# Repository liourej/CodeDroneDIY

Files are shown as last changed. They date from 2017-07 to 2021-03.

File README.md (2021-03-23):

# <p align="center">DIY flight controller from scratch</p>

<p align="center">
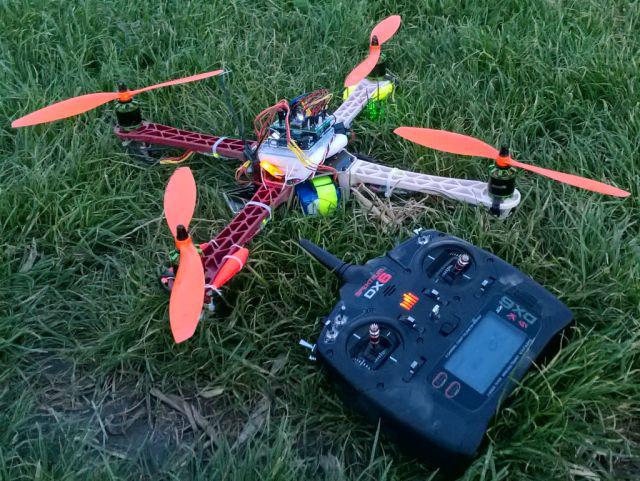
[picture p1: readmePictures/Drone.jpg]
    
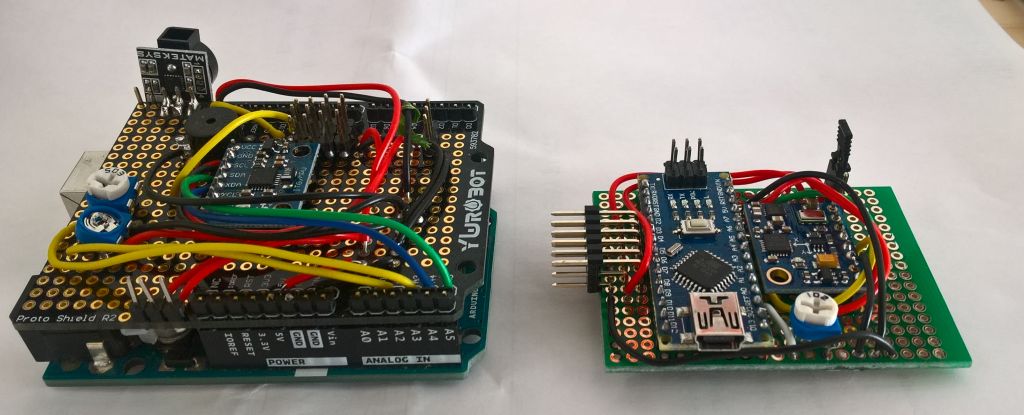
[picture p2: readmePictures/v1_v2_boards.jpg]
    
    Pictures: First hardware version using Arduino Uno board and second hardware version using Arduino Nano board
</p>

---------------------------Table of contents----------------------------

[**1. Introduction**](#intro)

1.1. Purpose

1.2. Progress state

1.3. Videos

[**2. Required sensors**](#requiredSensors)

[**3. Accro mode explained (aka manual)**](#accroMode)

3.1. Angle feedback

3.2. Speed stabilization

[**4. Angle mode explained (aka automatic leveling mode)**](#angleMode)

4.1. Angles and angular speeds feedback

4.2. Stabilization

[**5. Hardware configuration**](#hardwareConfiguration)

5.1. Components list

5.2. Connexions

[**6. Software setup**](#softwareSetup)

6.1 Using Arduino IDE

6.2 Using PlatformIO

6.3. Using Docker

[**7. Software detailed design**](#softwareDetailedDesign)

7.1 Source Code overview

7.2 The state machine

7.3 Radio reception

7.4 Motors speed control

7.5 Failsafe

[**8. Appendix**](#appendix)

8.1 My BenchTest

8.2 Exemple of First Person View configuration(FPV)

[**10. Glossary**](#glossary)

[**11. Bibliography**](#bibliography)

-------------------------------------------------------------------
## Warning

<p align="center">

</p>

Before starting this project, you must know that spinning propellers are very dangerous for your eyes and people around.
When using the benchtest indoor, you must wear large protective glasses, and set up a power limit.
For outside tests, choose a very large area, with nobody around.

<p align="center">
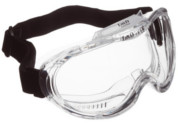
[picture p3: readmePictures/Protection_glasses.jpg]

</p>

## 1. Introduction 
### 1.1 Purpose
The aim of this project is to develop a very simple quadrirotor flight controller from scratch, using an Arduino and inertial sensors.
There is two benefits:
* to understand UAV flight stabilization
* to have our own system, with no limits for customization: you can add all the sensors you want.

In this project, the two main flight modes are addressed:
* Accrobatic mode (or manual mode): the simplest to code, but it requires flight skills
* Angle mode: more complex to implement, but easier to fly: UAV automatically goes back to
horizontal

I strongly advice to start by implementing the accrobatic mode, since a good accro mode will be a solid fundation
for angle mode, and it is easy and fast to implement.

### 1.2 Progress state
Releases have been successfully tested during flights tests: I have some nice flights in FPV on a
450mm frame, both in accro and angle modes.
BUT, this project is sometimes updated, mainly for code format, and unfortunately, I cannot realize flight tests for each submit.
So, I cannot garantee that the last commit will allow to flight without some corrections.

Note that you may also have to tune PID according to your configuration.

I advice you to use a large frame (450mm for exemple), because it is more stable, and I did not test the software on smaller frames.

### 1.3 Videos

<a href="https://www.youtube.com/watch?v=niiIYhLCFx0" target="_blank" rel="noopener noreferrer">Loop control indoor test</a>

<a href="https://www.youtube.com/watch?v=C8MZH-K4qus" target="_blank" rel="noopener noreferrer">Outdoor flight test</a>

## 2. Required sensors 

An IMU (aka MPU) is the only sensor needed for flight.

An « Inertial Measurement Unit » is a MEMS, "Microelectromechanical system", composed by a 3 axis gyroscope sensor, and 3 axis accelerometer sensor.

| IMU sensor | Function |Pros | Cons |
| --- | --- | --- | --- |
| Gyroscope | Measure angular speeds around each axis (°/sec) | Fast | Drift along time |
| Accelerometer | Measure linear acceleration on each axis (g) | Slow |  Noizy and not usable when UAV is moving |

<p align="center">
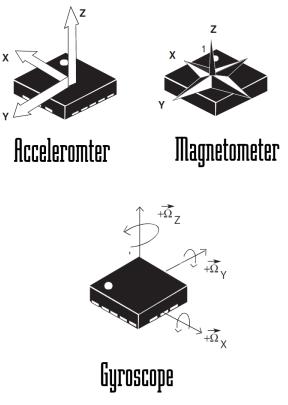
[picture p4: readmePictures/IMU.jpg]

</p>

## 3. Accro mode (aka manual) 

Accrobatic mode implements minimal stabilization algorithms to make flight possible. UAV is not able to auto-leveling, and pilot skills are required.

This mode is the required base for the angle mode, and is easier to realize: do not try to code angle mode if accro mode is not working fine.

### 3.1 Compute angle speed feedback

Accrobatic mode algorithm only needs UAV angular speeds and angular speed command as entry data. Angular speeds are computed from raw gyroscope data integration.

Exemple of pitch angle speed computation using gyroscopes:
```
// currentPitch = previousPitch + rawSensorPitch*loopTime
_pos[0] = _pos[0] + (accGyroRaw[0+3]/GyroSensitivity)*_loop_time;
```
### 3.2 Speed stabilization  

A closed-loop system is needed to control angular speed.

This system compares angular speed command to angular speed feedback, and computes a new motor power to apply.

<p align="center">
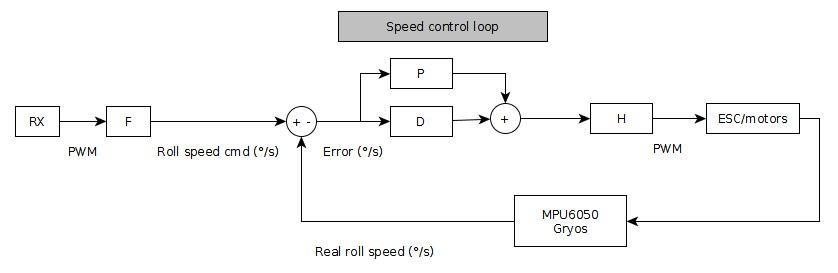
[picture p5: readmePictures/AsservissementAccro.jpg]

</p>

## 4. Angle mode (aka automatic leveling mode) 

It is a more sophisticated flight mode than the accrobatic mode: now, UAV is able to auto-level.

Auto-leveling mode entry data is UAV attitude: the angles from the horizontal (roll, pitch, yaw) and the angular speeds.

### 4.1 Compute angles and angular speeds feedback

Both angles speed and angles are required to compute reliable attitude angle feedback along time.

Both gyroscopes and accelerometers are involved.

#### 4.1.1 IMU gyroscopes

As seen previously, Angular speeds are computed from raw gyroscope data integration.

#### 4.1.1 IMU accelerometers

Attitude angles are computed from accelerations:

When UAV is not moving, or if it is moving at constant speed, accelerometers measure gravity, ie
vertical acceleration.
Angle between UAV and the gravity vector is computed by trigonometry.
Be carefull, this measure is faulty when UAV accelerates.

Exemple of pitch attitude angle computation using accelerometers:

```
_pos[0] = atan(accGyroRaw[1]/accGyroRaw[2]))*(180/PI);
```

#### 4.1.2 Data merging: the complementary filter

Complementary filter merges gyroscopes and accelerometers data, to get both sensors benefits, and to reduce theirs drawbacks:

* The gyroscope if fast but it drifts along time.

* Accelerometers are not fast enougth, they are noizy, and they are usable only when the UAV is not moving, and when UAV receive only earth acceleration.

The complementary filter mask their respective errors:

- A low-pass filter is applied on accelerometer data to filter the noize and the unwanted accelerations: these data are usefull on a long time period, fast changes have to be eliminated.
- A high-pass filter is applied on the gyrosope data: these data are usefull on short time period, but they drift and accumulate errors on long time periods.

<p align="center">
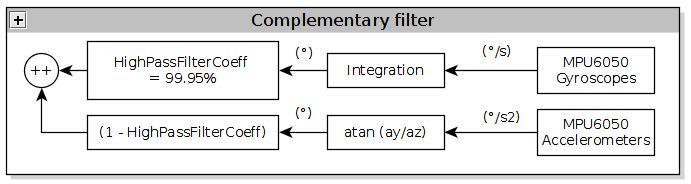
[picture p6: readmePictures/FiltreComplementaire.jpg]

</p>

**Coding exemple**

  ```
 _pos[0] = HighPassFilterCoeff*(_pos[0] + (accGyroRaw[0+3]/GyroSensitivity)*_loop_time) +
 (LowPassFilterCoeff)*((atan(accGyroRaw[1]/accGyroRaw[2]))*(180/PI));
```

Note: LowPassFilterCoeff = 1 - HighPassFilterCoeff

**Coefficients computation**

HighPassFilterCoeff is computed from the Time constant.

Time constant is a compromise between UAV acceleration filtering, and gyroscopes drift:
* Too low, accelerometer noize are not eliminated
* Too high, gyroscopes drift is not compensated

```
timeConstant = (HighPassFilterCoeff*dt) / (1-HighPassFilterCoeff)
=> HighPassFilterCoeff = timeConstant / (dt + timeConstant)
```

Time constant in this project is set to 5 milliseconds. It implies a coefficient "HighPassFilterCoeff" of 0.9995 for a loop time of 2.49 ms.

**Note:** More efficient filters like the Kalman one are used in UAV, but they are more complicated to understand, and we want a very simple DIY software!

### 4.2 Stabilization

A double closed-loop system is needed to control attitude angles. It consists of a speed closed-loop [like the one in the accro mode], inside a position closed-loop.

This system compares angle command to angle feedback, and computes a new motor power to apply. Angular feedback is computed using a complementary filter to merge gyroscope dans accelerometer data.

The pilot controls each attitude angle, and if transmitter sticks are centered, command is 0°, and UAV automatically goes back to horizontal.

<p align="center">
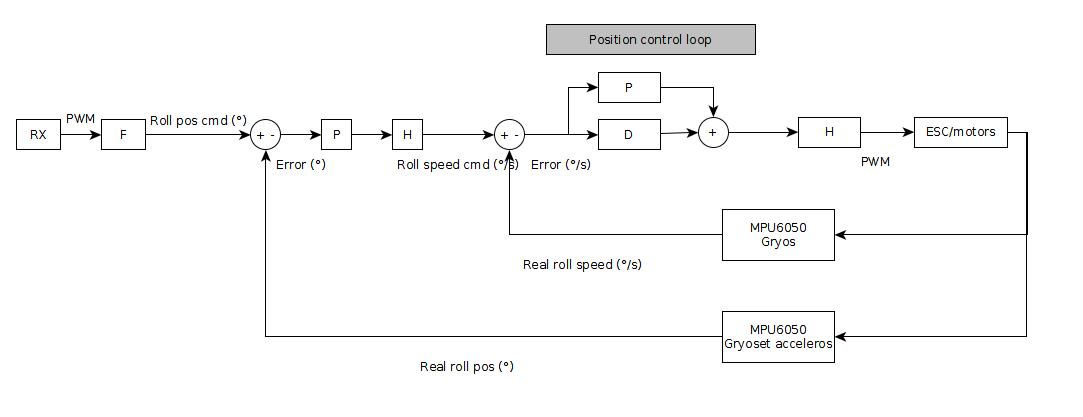
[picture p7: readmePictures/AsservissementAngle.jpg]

</p>

## 5. Hardware configuration 

### 5.1 Components list

As exemple, my hardware configuration for a 450mm quad:

| Component | Reference |
| --- | --- |
| **Microcontroller board** | Arduino Nano/Uno (ATmega328P MCU) |
| **ESC** | Afro 20A-Simonk firmware 500Hz, BEC 0.5A 1060 to 1860 us pulse width |
| **Motors** | Multistar 2216-800Kv 14 Poles - 222W Current max: 20A Shaft: 3mm 2-4S|
| **Propellers** | 10x4.5 SF Props 2pc CW 2 pc CCW Rotation (Orange) |
| **Battery** | Zippy Flightmax 3000mAh 4S |
| **Receiver** | OrangeRx R617XL CPPM DSM2/DSMX 6 ch |
| **IMU** | MPU6050 (GY-86 breakout board)|
| **Compass** | HMC5883L (GY-86 breakout board) |
| **Buzzer** | Matek lost model beeper - Built-in MCU |
| **Frame** | Diatone Q450 Quad 450 V3. 450 mm wide frame choosen for better stability and higher autonomy (the lower the size, the lower the stability).|

### 5.2 Connexions
TODO: add receiver in schematic

**Full view:**

<p align="center">
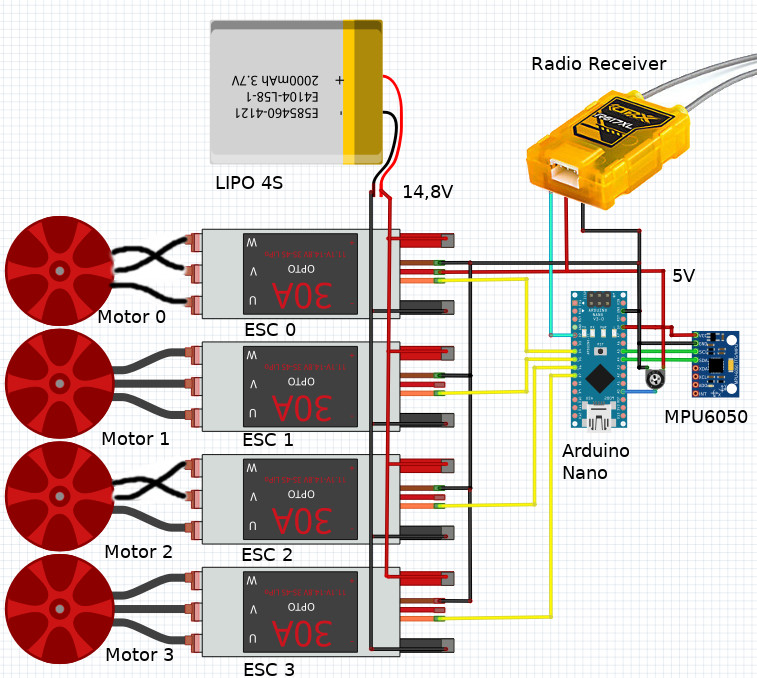
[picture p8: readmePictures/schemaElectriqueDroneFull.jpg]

</p>

**Zoomed view:**

<p align="center">
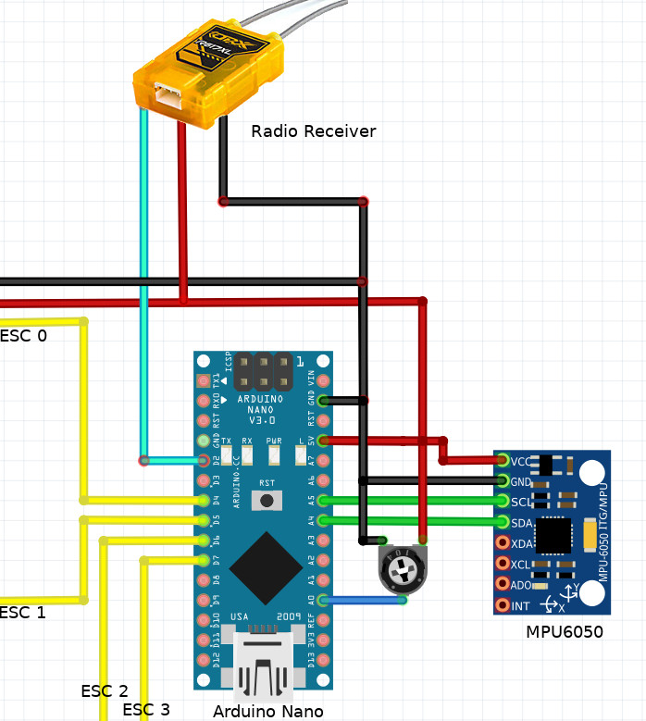
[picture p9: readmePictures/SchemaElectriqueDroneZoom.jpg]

</p>

| Arduino pin | Component |
| --- | --- |
| PD2 | receiver |
| PD4 | ESC0 |
| PD5 | ESC1 |
| PD6 | ESC2 |
| PD7 | ESC3 |
| PC0 | potentiometer |
| PC4 | SDA MPU6050 |
| PC5 | SCL MPU6050 |

<p align="center">
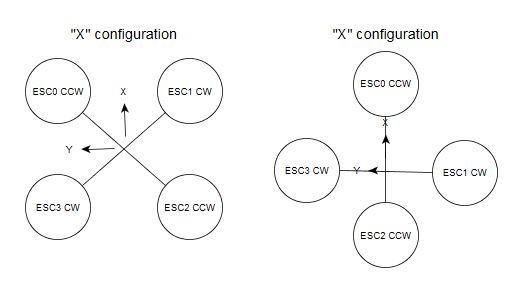
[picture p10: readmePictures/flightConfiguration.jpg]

</p>

## 6. Software setup 

### 6.1 Using Arduino IDE
With minor modifications, project can be build using Arduino IDE:
* rename "main.cpp" to "CodeDroneDIY.ino"
* copy all source files from "CodeDroneDIY/src" to "CodeDroneDIY"
* launch and compile "CodeDroneDIY.ino" using Arduino IDE

### 6.2. Using Visual Studio Code IDE and PlatformIO

* Install Visual Studio code

* Start VSCode and click on "Extensions" icon

* Install PlatformIO IDE

### 6.3. Using  Linux terminal and PlatformIO
PlatformIO is an open source ecosystem for IoT development.

#### 6.2.1. PlatformIO installation
```sudo apt-get update
sudo apt-get install python-pip
sudo pip install --upgrade pip && sudo pip install -U platformio==3.5.2
platformio platform install atmelavr --with-package=framework-arduinoavr
platformio lib install MPU6050
pio lib install "I2Cdevlib-MPU6050"
```

Optional, for code format:

```sudo apt-get install -y clang-format```

#### 6.2.2. Build project
```platformio run```

#### 6.2.3. Flash target
```platformio upload --upload-port/ttyACM0 ```

#### 6.2.4. Run unit tests

```
platformio test -e uno --verbose
```

### 6.4. Using Docker and PlatformIO
The development tool "Docker" is a container platoform: it is a stand-alone, executable package
of a piece of software that includes everything needed to run it: code, runtime, system tools,
 system libraries, settings. It isolates software from its surroundings.
* Install Docker
* Move inside docker's folder: ```cd docker```
* Build docker image: ```make image```
* Format code: ```make format-all```
* build project: ```make build-codedronediy```

## 7. Software detailed design 

### 7.1 Source code overview

<p align="center">
<img src="/readmePictures/DiagrammeUML.jpg"/>
</p>

**StateMachine folder:**

| File      | Description      |
| -------------- | -------------- |
| StateMachine.h | Contains current state |
| states/IState.h | Interface for the states (mother class)|
| states/AccroMode.cpp/h | Computes stabilization for accro mode |
| states/AngleMode.cpp/h | Computes stabilization for angle mode|
| states/Disarmed.cpp/h | Sets motors to idle |
| states/Initializing.cpp/h | Computes offsets |
| states/Safety.cpp/h | Sets motors to idle |

**Stabilization folder:**

| File      | Description      |
| -------------- | -------------- |
| hardware/InertialMeasurementUnit.cpp/h | Read roll, pitch, yaw angles from MPU6050 |
| hardware/MotorsSpeedControl.cpp/h | Manage an ESC: PWM to set |
| hardware/RadioReception.h | Receives CPPM signal acquisition using INT0 |
| Stabilization.cpp/h | Computes and apply new command from receiver sticks and current attitude |
| ControlLoop.cpp/h | Proportionnal, integral, derivative loop correction |

**customLibs folder:**

| File      | Description      |
| -------------- | -------------- |
| CustomMath.h | Mathermatical functions: mean and delta max computations|
| CustomTime.h | To measure loop time and elapsed time |
| CustomSerialPrint.h | Custom serial print to enable or disable printing|

### 7.2 The state machine

Due to security reasons, the UAV cannot start running with a flight mode enabled. Five states are defined to enable or disable flight mode safely. These states are ruled by a statemachine.

The five StateMachine states:

<p align="center">
<img src="/readmePictures/MachineEtats.jpg"/>
</p>

| State      | Description      |
| -------------- | -------------- |
| Initialization | UAV must be on the ground, horizontal, and not moving. Sensors offsets are computed. Then, if receiver switch is disarmed, the system changes to the next state. |
| Disarmed | Throttle is disabled. When the receiver switch is set to a flight mode, the system changes to the corresponding state.|
| AngleMode/AccroMode | Throttle is enabled, flight can start. After 5 seconds of power idle, the system is set to "safety" state. |
| Safety | Throttle command is disabled and power is cut. To re-arm, switch to disarmed, then choose the flight mode accroMode or angleMode |

### 7.3. Radio reception

A CPPM receiver is used to fly the UAV using a remote control.

CPPM (Pulse Position Modulation) reception  allows to receive all channels using only one entry pin. Each rising edge correpond to the end of the previous channel impulsion, and at the beginning of the next channel impulsion.
Elapsed time between two rising edge correspond to the pulse width of a given channel.

<p align="center">
<img src="/readmePictures/CPPM.jpg"/>
</p>

In this projet, each pulse width is measured using INT0, and then stored in the correponding channel of an array.

### 7.4 Motors speed control

Each motor is controlled by an ESC. The microcontroller drives the 4 ESC.

<p align="center">
<img src="/readmePictures/Afro20Amp-ESC.jpg" width="20%"/>
</p>

Motor speed is tuned by modifying the pulse width on the ESC signal wire. A pulse must be send at least every 20ms.

* Max motor speed is set by a pulse of 1860ms

* Motor is stopped by a pulse of 1060ms

All speeds between this two values are possible.

Each timer1 interrupt call the function "SetMotorsSpeed", which generate a falling edge on the previous motor and a rising edge on the current motor:

<p align="center">
<img src="/readmePictures/MotorsControl.jpg" width="60%"/>
</P>

### 7.5 Failsafe

For security, you must set the failsafe to cut motors power when radio link is lost.

To set the failsafe:
1. Put transmitter sticks in the configuration wanted when reception is lost
2. Bind the receiver with the transmitter

Transmitter configuration used during the « bind » operation defines the « failsafe. »

## 8. Appendix 

### 8.1 The benchtest

<p align="center">
<img src="/readmePictures/BenchTest01.jpg" width="40%"/>
</p>

### 8.2 FPV - First Person View  

My cheap configuration:

| Component      | Reference      |
| -------------- | -------------- |
| **Googgles** | Quanum DIY FPV Goggle V2 Pro |
| **Googgles battery** | 1000 mAh 3S |
| **Receiver** | Eachine RC832 Boscam FPV 5.8G 48CH Wireless AV Receiver  |
| **Receiver antenna** | DYS FPV 5.8G Antenna 4dBi Mushroom Antenna RHCP TX RX |
| **Camera** | Foxeer XAT600M HS1177 600TVL CCD 2.8MM IR Mini FPV Camera IR Blocked 5-22v |
| **Camera antenna** | Realacc 5.8G 5dBi 50W RHCP Omnidirectional 3 Leaf Clover FPV Antenna Red |
| **Video transmitter** | Upgrade Aomway Mini 5.8Ghz 200mW 32CH AV Wireless Transmitter Module |

## 10. Glossary 

**ESC** Electronic Speed Control

**PID** It is a Proportionnal Integral Derivative control loop

**IMU** Inertial Measurement Unit

**MPU** Motion Processor Unit

**FPV** First Person View

## 11. Bibliography 

* Arduino

https://www.arduino.cc/en/Reference/Libraries.html

https://www.arduino.cc/en/Reference/HomePage

* PWM

https://librepilot.atlassian.net/wiki/display/LPDOC/PWM,+PWMSync,+Oneshot+Output

http://forum.arduino.cc/index.php?topic=46487.0

* PPM

http://frskytaranis.forumactif.org/t4426-tuto-pwm-cppm-ccpm-ppm-s-bus-s-port-kesako

* PID

http://www.fpv-passion.fr/docteur-pid/

* Quadricopter

https://www.mondrone.net/fabriquer-quadricoptere-la-propulsion/

* Data processing

https://ericjformanteaching.wordpress.com/2013/10/08/smoothing-sensor-input/

* Data merging

http://www.mouser.fr/applications/sensor_solutions_mems/

http://www.pieter-jan.com/node/11

* Programme python

Andy BAKER

http://pythonfiddle.com/andy-baker-quadcopter/

* Vibrations

http://ardupilot.org/plane/docs/common-vibration-damping.html

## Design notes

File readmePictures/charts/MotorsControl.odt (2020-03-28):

Motor0 Motor1 Motor2 Motor3 Motor0 Timer Interrupt Timer Interrupt Timer Interrupt Timer Interrupt Timer Interrupt Timer Interrupt ticks ticks ticks PD4 (V) PD5 (V) PD6 (V) PD7 (V) ticks Motor1 Timer Interrupt

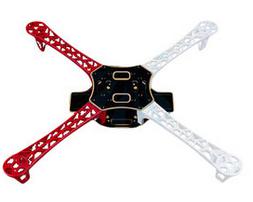
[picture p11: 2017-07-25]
readmePictures/Chassis.jpg

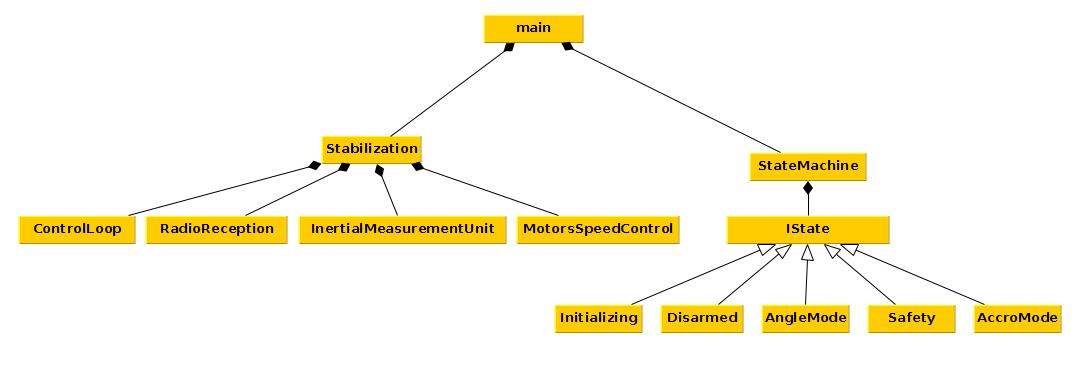
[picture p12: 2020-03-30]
readmePictures/DiagrammeUML.jpg

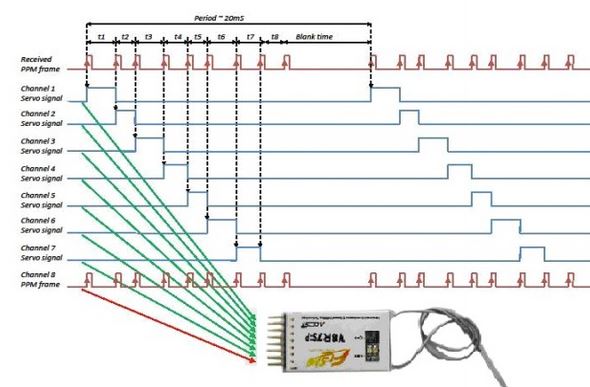
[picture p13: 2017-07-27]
readmePictures/CPPM.JPG

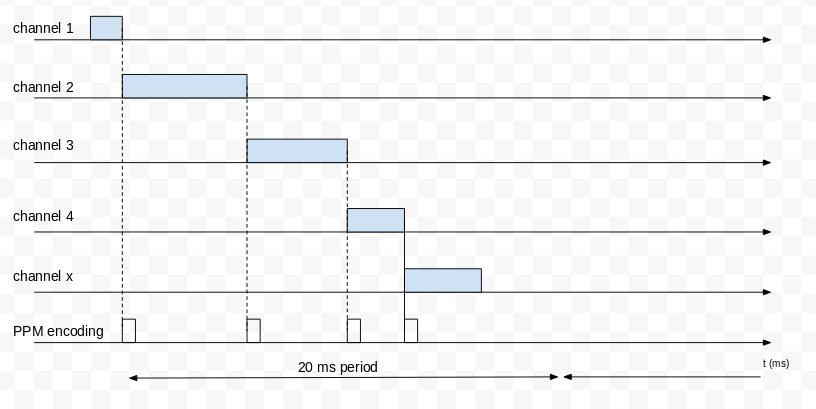
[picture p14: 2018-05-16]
readmePictures/CPPM.jpg

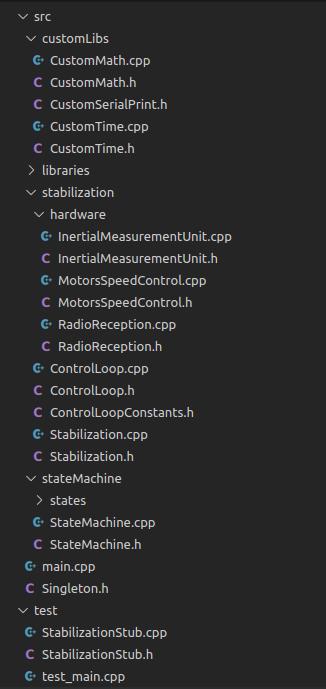
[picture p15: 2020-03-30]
readmePictures/CodeTree.jpg

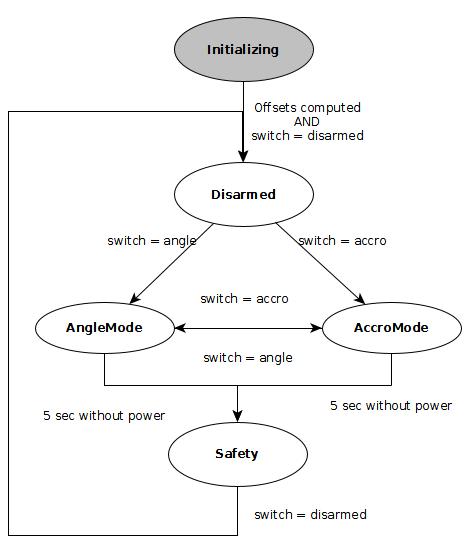
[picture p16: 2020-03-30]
readmePictures/MachineEtats.jpg

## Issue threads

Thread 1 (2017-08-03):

Wiring

2black0, 2017-08-03:
Can you share the wiring?
or any board can be to test this directly?

liourej, 2018-05-02:
The code can be run on any board using ATmega328P (Arduino Uno, Nano).
Wiring:

Arduino pin | Component
PD2 | receiver
PD4 | ESC0
PD5 | ESC1
PD6 | ESC2
PD7 | ESC3
PC0 | potentiometer
PC4 | SDA MPU6050
PC5 | SCL MPU6050

Closed 2018-05-02.

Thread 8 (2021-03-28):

Raspberry Pico

pschatzmann, 2021-03-28:
Thanks for your project. this is great work.

I am trying to use your project on a Raspberry Pico. The only AVR specific functionality is in MotorsSpeedControl so I need to provide an alternative implementation.

I have one small doubt with the  void MotorsSpeedControl::UpdateSpeed(int _id, float _PWM) method.

Is the _PWM argument the pulse width (in the range of MIN_POWER - MAX_POWER ? Or is it something else ?

The naming and data type got me a little bit confused...

pschatzmann, 2021-03-29:
I have an implementation now: https://github.com/pschatzmann/pico-arduino/blob/main/examples/codedronediy
I hope I did not get it wrong...

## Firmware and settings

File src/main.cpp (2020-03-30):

#ifndef UNIT_TEST
#include <avr/wdt.h>
#include <math.h>

#include "customLibs/CustomTime.h"
#include "stabilization/hardware/RadioReception.h"
#include "stabilization/Stabilization.h"
#include "stateMachine/StateMachine.h"

CustomTime time;
Stabilization stabilization;
StateMachine stateMachine;
void PrintConfig();

// Initialiaze all sensors and communication pipes
void setup() {
    CustomSerialPrint::begin(230400); // Console print: initialize serial communication

    stabilization.Init();
    time.Init();
    stateMachine.Init();

    wdt_enable(WDTO_1S); // Set watchdog reset
    PrintConfig();
}

// Main loop
void loop() {
    float loopTimeSec = 0.0;
    uint16_t loopNb = 0;
    float meanLoopTime = 0.0;

    loopTimeSec = time.GetloopTimeMilliseconds();

    // State Machine Initializing -> Ready -> AngleMode/AccroMode -> Safety -> Disarmed -> AngleMode/AccroMode
    stateMachine.Run(loopTimeSec);

    // Compute mean loop time and complementary filter time constant
    int flyingMode = stabilization.GetFlyingMode();
    if ((flyingMode == angleMode) || (flyingMode == accroMode)) {
        if (!stabilization.IsThrottleIdle()) {
            time.ComputeMeanLoopTime(loopTimeSec, meanLoopTime, loopNb);
        }
    }
    wdt_reset();
}

void PrintConfig() {
    if ((stabilization.GetMotorsMaxPower() == 1860)
        && (stabilization.GetMotorsMaxThrottle() >= (1860 * 0.8)))
        CustomSerialPrint::println(
                F("!!!!!!!!!!!!!!!!!!!!FLYING MODE "
                  "POWER!!!!!!!!!!!!!!!!!!!!!!!!!!!!!!!!!!!! "));
    else if ((stabilization.GetMotorsMaxPower() <= 1300))
        CustomSerialPrint::println(F("DEBUG MODE POWER!!! "));
    else
        CustomSerialPrint::println(F("UNEXPECTED POWER "));

    CustomSerialPrint::print(F("MAX_POWER: "));
    CustomSerialPrint::print(stabilization.GetMotorsMaxPower());
    CustomSerialPrint::print(F(" MAX_THROTTLE_PERCENT: "));
    // CustomSerialPrint::println(stabilization.GetMotorsMaxThrottlePercent());
    CustomSerialPrint::println(F("Setup Finished"));
}
#endif

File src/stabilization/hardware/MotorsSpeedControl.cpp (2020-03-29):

#include "MotorsSpeedControl.h"

int MotorsSpeedControl::currMotor = -1;
uint16_t MotorsSpeedControl::motorsTicks[nbMotors] = {0, 0, 0, 0};

void MotorsSpeedControl::Init() {
    // Set motors pin PD4, PD5, PD6, PD7 as outputs
    DDRD |= (1 << DDD7)| (1 << DDD6)| (1 << DDD5)| (1 << DDD4);
    InitTimer1();
    Idle();
}

// Timer interrupt to set PWM to motors controllers
typedef enum { _timer1, _Nbr_16timers } timer16_Sequence_t;

static inline void handle_interrupts(timer16_Sequence_t timer, volatile uint16_t *TCNTn,
                                     volatile uint16_t *OCRnA) {
    MotorsSpeedControl::ApplySpeed(TCNTn, OCRnA);
}

// Timer 1 is use to drive motors using PWM
SIGNAL(TIMER1_COMPA_vect) {
    handle_interrupts(_timer1, &TCNT1, &OCR1A);
}

// Timer 1 is use to drive motors using PWM
void MotorsSpeedControl::InitTimer1() {
    TCCR1A = 0;         // normal counting mode
    TCCR1B = _BV(CS10); // no prescaler
    TCNT1 = 0;          // clear the timer count
    OCR1A = usToTicks(MIN_POWER);

    TIFR1 |= _BV(OCF1A);   // clear any pending interrupts;
    TIMSK1 |= _BV(OCIE1A); // enable the output compare interrupt
}

void MotorsSpeedControl::Idle() {
    for (int id = 0; id < nbMotors; id++)
        motorsTicks[id] = usToTicks(MIN_POWER);
}

void MotorsSpeedControl::UpdateSpeed(int _id, float _PWM) {
    if (_PWM < MIN_POWER) {
        motorsTicks[_id] = usToTicks(MIN_POWER);
    } else if (_PWM > MAX_POWER) { // Check max power
        CustomSerialPrint::println(F("WARNING, MAX POWER REACHED!!"));
        motorsTicks[_id] = usToTicks(MAX_POWER);
    } else {
        motorsTicks[_id] = usToTicks(_PWM);
    }
}

// Set a falling edge for the previous motor, and a rising edge for the current motor
// Motor speed is managed by the pulse with: the larger the high level is, the faster the motor run
void MotorsSpeedControl::ApplySpeed(volatile uint16_t *TCNTn, volatile uint16_t *OCRnA) {
    static bool firstLoop = true;
    if (firstLoop) {
        currMotor = 0;
        PORTD = B00010000;
        firstLoop = false;
    }

    if (currMotor == Motor0) { // Rising edge for Motor0, and falling edge for Motor3
        PORTD ^= B00110000; // Reset pin PD4 and set pin PD5 using XOR
        *OCRnA = motorsTicks[currMotor + 1]; // When TCNTn matches OCRnA, an output compare interrupt is thrown.
    } else if (currMotor == Motor1) {// Rising edge for Motor1, and falling edge for Motor0
        PORTD ^= B01100000; // Reset pin PD5 and set pin PD6 using XOR
        *OCRnA = motorsTicks[currMotor + 1];// When TCNTn matches OCRnA, an output compare interrupt is thrown.
    } else if (currMotor == Motor2) {// Rising edge for Motor2, and falling edge for Motor1
        PORTD ^= B11000000; // Reset pin PD6 and set pin 7 using XOR
        *OCRnA = motorsTicks[currMotor + 1];// When TCNTn matches OCRnA, an output compare interrupt is thrown.
    } else {// Rising edge for Motor3, and falling edge for Motor2
        PORTD ^= B10010000; // Reset pin PD7 and set pin PD4 using XOR
        currMotor = -1;
        *OCRnA = motorsTicks[currMotor + 1];// When TCNTn matches OCRnA, an output compare interrupt is thrown.
    }
    *TCNTn = 0; // Reset timer counter
    currMotor++;
}

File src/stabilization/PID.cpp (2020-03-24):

#include "PID.h"
void PID::SetGains(const float _params[4]) {
    G = _params[0];
    Kp = _params[1];
    Kd = _params[2];
    Ki = _params[3];
}

void PID::Reset() {
    errorPrev = 0;
    integrator = 0;
}

int PID::ComputeCorrection(float _cmd, float _pos, float _loopTime) {
    error = _cmd - _pos;
    integrator = integrator + error;
    int correction =
            (int)(G * (Kp * error + Kd * ((error - errorPrev) / (_loopTime)) + Ki * integrator));

    errorPrev = error;

    // Correction in us
    return correction;
}

void PID::PrintGains(void) {
    Serial.print("G: ");
    Serial.print(G);
    Serial.print(" Kp: ");
    Serial.print(Kp);
    Serial.print(" Kd: ");
    Serial.print(Kd);
    Serial.print(" Ki: ");
    Serial.println(Ki);
}

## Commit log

2017-05-23 Correct wrong pitch correction sign
2017-05-23 Correct negative sign on pitch speed
2017-05-26 Use switch H to activate yaw PID
2017-05-28 After flight fail, set much better PID coeff
    [Reception.h]
2017-05-28 Add loop mean comp: PID coeff depends itgit add . (1.7ms in this version)
2017-05-29 Adjust angle mode PID parameters
2017-06-01 Add missing yaw reset
2017-06-03 Release for flight test - TODO: Investigate why - on pitch pos
2017-06-11 Add a safety power cut on 5th channel and code cleaned
2017-06-12 Add safety switch with safety cut after 5sec. Need cleaning!
2017-06-13 Create a state machine to encapsulate safety cut code
2017-06-24 Add buzzer activated by H switch
2017-06-27 Add IMU self-test to check IMU is working
2017-07-05 Move PID init into state machine
2017-07-08 IMU checking before flight working fine.
2017-07-08 Buzzer working with motor PWM timer at the same time
2017-07-08 Correct sign in pitch attitude computation
    [GetPosition.cpp]
2017-07-09 Complementary filter coef proportional to quadri moving probability
2017-07-09 Compute a better filter time constant. Remove changing constant.
2017-07-14 Much better filter time constant: 5sec (coeff 0.9995)
2017-08-10 Correct out of range array bug
    [Reception.h]
2017-08-19 Linux Arduino makefile working
2017-08-26 New Arduino Nano board
2017-09-02 Add a percentage thsld on throttle cmd, independant from max motor pwr thsld
2017-10-26 Update readme schematics
2017-10-28 Correct but in function used to reset PID when throttle idle
2017-10-28 Rem auto baro detection: not working because no I2C timeout
    [Attitude.cpp]
2017-10-28 Tune PIDs for 220mm racer frame
2017-10-29 Add potentiometer on A0 to tune yaw Kp on the field
2018-03-07 Add electrical schematic (WIP)
2018-05-02 Restore IMU checking at startup
2018-05-02 Create a class for IMU check at startup
2018-05-16 Create function to set sensors sensitivity
2018-05-16 Draw CPPM schematic
2020-03-24 Use a static class to store PID constants
2020-03-27 StateMachine tests working, but IMU not
2020-03-27 Encapsulate Serial.print to add print levels (DEBUG, etc)
2020-03-28 Use static const int to define motors pins
2020-03-29 Refactoring: Move interruptions declaration in each corresponding class
2020-03-30 Update electrical schematics
    [SchemaElectrique.fzz]
